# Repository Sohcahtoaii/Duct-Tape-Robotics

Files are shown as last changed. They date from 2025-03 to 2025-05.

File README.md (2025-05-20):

Robot pour la RoboCup – Catégorie Rescue Line Junior

Les fichiers de conception mécanique (CAO) ainsi que ceux de la carte électronique sont disponibles dans ce dépôt.

Une liste complète des pièces utilisées, avec des liens vers les composants, est également fournie.
Cependant, il est fortement recommandé de vérifier les empreintes (footprints) et les dimensions avant tout achat, afin d’éviter les erreurs de compatibilité.

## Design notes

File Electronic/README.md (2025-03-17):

Carte électronique du robot, liste des composants et librairy avec les componsants utilisés

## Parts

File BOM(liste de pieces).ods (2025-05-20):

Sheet: Feuille 1
Mecanique | ref | ref schema | nb | prix | cumul | lien
Roulement à billes 686-ZZ |  | nf | 1 | 2.9 | 2.9
Vis m3 |  | nf | 1 | 1.59 | 1.59
Insert a chaud |  | nf | 2 | 1.95 | 3.9
 |  |  |  |  | 0
Carte mere |  |  |  |  | 0
Batterie/ connecteur |  |  |  |  | 0
XT60PW male |  | J7 | 1 | 3.59 | 3.59 | Lien (https://fr.aliexpress.com/item/1005005383209263.html?mp=1)
led allumage | smd 0805 | D7 | 1 | 2.99 | 2.99 | Lien (https://fr.aliexpress.com/item/1005005226854182.html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)
Resistance | smd 0805 | R8 | 1 | 3.95 | 3.95 | Lien (https://fr.aliexpress.com/item/1005006823361841.html?sourceType=1)
Alim 5v |  |  |  |  | 0
TPS5431DDA | regulateur linéaire | U1 | 1 | 4.49 | 4.49 | Lien (https://fr.aliexpress.com/item/1005007968402584.html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)
Condensateur | smd0805 10nF78mOhm | C1 | 1 |  | 0 | Lien (https://fr.aliexpress.com/item/1005002782324319.html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)
Condensateur | smd 0805 22uF2mOhm | C6/C10 | 2 |  | 0 | Lien (https://fr.aliexpress.com/item/1005002782324319.html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)
Condensateur polarisé | CP_Elec_10x12.6 330uF25mOhm | C2 | 1 | 3.6 | 3.6 | Lien (https://fr.aliexpress.com/item/1005002964957462.html?productId=1005002964957462)
Inductor | 15uH32mOhm | L2 | 1 | 1.43 | 1.43 | Lien (https://fr.aliexpress.com/item/1005006170108324.html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)
Schottky diode | 450mV3A | D1 | 1 | 2.34 | 2.34 | Lien (https://fr.aliexpress.com/item/1005008728420045.html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)
Resistance | smd 0805 10K | R1 | 1 |  | 0 | Lien (https://fr.aliexpress.com/item/1005006823361841.html?sourceType=1)
Resistance | smd 0805 3.24K | R2 | 1 |  | 0 | Lien (https://fr.aliexpress.com/item/1005006823361841.html?sourceType=1)
Alim3,3v |  |  |  |  | 0
TPS5431DDA | regulateur linéaire | U3 | 0 | 4.49 | 0 | Lien (https://fr.aliexpress.com/item/1005007968402584.html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)
Condensateur | 4.7uF3mOhm | C5/c8/c9 | 1 |  | 0 | Lien (https://fr.aliexpress.com/item/1005002782324319.html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)
Condensateur | 10nF78mOhm | C3 | 1 |  | 0 | Lien (https://fr.aliexpress.com/item/1005002782324319.html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)
Condensateur polarisé | 560uF 9mOhm | C4 | 1 | 2.17 | 2.17 | Lien (https://fr.aliexpress.com/item/1005006235242712.html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)
Inductor | 10uH31mOhm | L1 | 1 | 1.6 | 1.6 | Lien (https://fr.aliexpress.com/item/4001191021559.html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)
Schottky diode | 500mV3A | D2 | 1 | 1.74 | 1.74 | Lien (https://fr.aliexpress.com/item/1005008728420045.html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)
Resistance | smd0805 10k | R3 | 1 |  | 0 | Lien (https://fr.aliexpress.com/item/1005006823361841.html?sourceType=1)
Resistance | smd0805 5,9k | R4 | 1 |  | 0 | Lien (https://fr.aliexpress.com/item/1005006823361841.html?sourceType=1)
 |  |  |  |  | 0
Port usb |  |  |  |  | 0
port usb | USB_C_ N 16Pin |  | 1 | 1.78 | 1.78 | Lien (https://fr.aliexpress.com/item/1005007419369264.html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)
Resistance | 0805 5,1k | r5/r6 | 2 |  | 0 | Lien (https://fr.aliexpress.com/item/1005006823361841.html?sourceType=1)
Bidirectional transient-voltage-suppression diode | bidirectional tvs LESD5D5.0CT1G | D4/D5/D6 | 3 | 2.99 | 8.97 | Lien (https://fr.aliexpress.com/item/1005007089592096.html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)
Schottky diode | B130-E3 | D3 | 1 | 5.34 | 5.34 | Lien (https://fr.aliexpress.com/item/1005008617442777.html?mp=1)
Bouton boot |  |  |  |  | 0
push button traversant | push button | SW1 | 1 | 0.96 | 0.96 | Lien (https://fr.aliexpress.com/item/1005006046180384.html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)
Condensateur | 1uF/10V/10%/X5R/C0603 | C12 | 1 |  | 0 | Lien (https://fr.aliexpress.com/item/1005002782324319.html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)
Resistance | 10k smd0805 | R7 | 1 |  | 0 | Lien (https://fr.aliexpress.com/item/1005006823361841.html?sourceType=1)
Bouton rst |  |  |  |  | 0
push button traversant | push button | SW2 | 1 |  | 0 | Lien (https://fr.aliexpress.com/item/1005006046180384.html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)
Condensateur | 1uF/10V/10%/X5R/C0603 | C7 | 1 |  | 0 | Lien (https://fr.aliexpress.com/item/1005002782324319.html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)
Resistance | 10k smd0805 | R19 | 1 |  | 0 | Lien (https://fr.aliexpress.com/item/1005006823361841.html?sourceType=1)
Mesure batterie |  |  |  |  | 0
Resistance | 100k smd 0805 | R9 | 1 |  | 0 | Lien (https://fr.aliexpress.com/item/1005006823361841.html?sourceType=1)
Resistance | 27k smd 0805 | R10 | 1 |  | 0 | Lien (https://fr.aliexpress.com/item/1005006823361841.html?sourceType=1)
Condensateur | 100nF | C11 | 1 |  | 0 | Lien (https://fr.aliexpress.com/item/1005002782324319.html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)
Driver |  |  |  |  | 0
PinSocket_1x07_P2.54mm_Vertical_SMD_Pin1Righ |  |  | 1 | 2.62 | 2.62 | Lien (https://fr.aliexpress.com/item/1005006319376319.html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)
PinSocket_1x07_P2.54mm_Vertical_SMD_Pin1left |  |  | 1 | 2.62 | 2.62 | Lien (https://fr.aliexpress.com/item/1005006319376319.html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)
Capteur |  |  |  |  | 0
Connecteur 11 pin molex picoblade |  | J8 | 1 | 5.59 | 5.59 | Lien (https://fr.aliexpress.com/item/1005006111477998.html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)
Connecteur 4 pin molex picoblade |  | J2 | 1 | 1.35 | 1.35 | Lien (https://fr.aliexpress.com/item/1005006027334406.html?mp=1)
Connecteur 7 pin molex picoblade |  | J9/J10 | 2 | 1.55 | 3.1 | Lien (https://fr.aliexpress.com/item/1005006027334406.html?mp=1)
Connecteur 8 pin molex picoblade |  | J11 | 1 | 1.55 | 1.55 | Lien (https://fr.aliexpress.com/item/1005006027334406.html?mp=1)
capteur de couleur |  |  | 2 | 2.12 | 4.24
capteur de ligne | QTRX-MD-08A |  | 1
Moteur |  |  | 1 | 26.75 | 26.75
bornier a vis |  | j3/j4 | 2 | 1.41 | 2.82 | Lien (https://www.aliexpress.com/store/1102861072?spm=a2g0o.cart.0.0.24a2378dIC0mR0)
Traitement |  |  |  |  | 0
esp32 s3 wroom 2 | esp32 s3 wroom 2 | U2 | 1 | 19.52 | 19.52 | lien (https://www.mouser.fr/ProductDetail/Espressif-Systems/ESP32-S3-WROOM-1-N8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)
 |  |  |  |  | 123.5

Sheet: Feuille 2
Support Moteur | 2 | Impression 3D
Cache moteur | 2 | Impression 3D
Support roue libre | 2 | Impression 3D
Châssis haut | 1 | Découpe laser
Châssis bas | 1 | Découpe laser
Axe roue arriere | 2(pièce de rechange conseillé) | Impression 3D
roue holonome GTF robot | 2 | Acheté
Roue avant personnalisé | 2 | Usinage CNC Moulage silicone (Département GMP iut Bordeaux)
adaptateur axe roue avant part 1 | 2 | Impression 3D
adaptateur axe roue avant part 2 | 2 | Impression 3D
Support capteur de ligne | 1 | Impression 3D
Support capteur ultrason | 1 | Impression 3D
Support Batterie | 1 | Impression 3D
Fermeture support batterie | 1 | Impression 3D
Roulement a bille SBC686ZZ | 4 | Acheté
Entretoise M/F 45mm m3 | 4 | Acheté
Entretoise M/F 15mm m3 | 4 | Acheté
Vis M3x6 | env.70 | Acheté
Vis M3x8 | env.10 | Acheté
Insert à chaud M3 | env.40 | Acheté
Moteur Modelcraft RB350030-0A101R 1:30 | 2 | Acheté

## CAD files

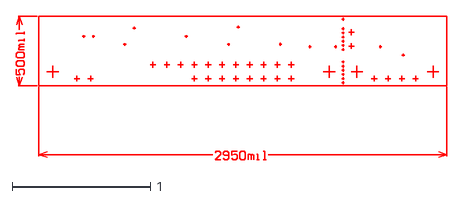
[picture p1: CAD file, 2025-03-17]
CAO/Used model/irs02a02-drill.dxf
3.11 x 1.04

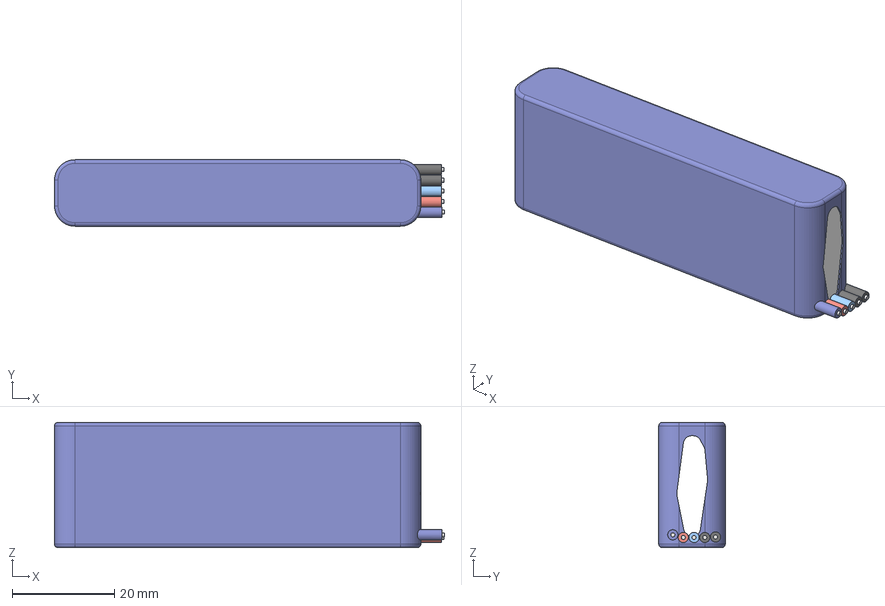
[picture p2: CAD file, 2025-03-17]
CAO/Used model/Battery.step
76.2 x 13.0 x 24.5 mm

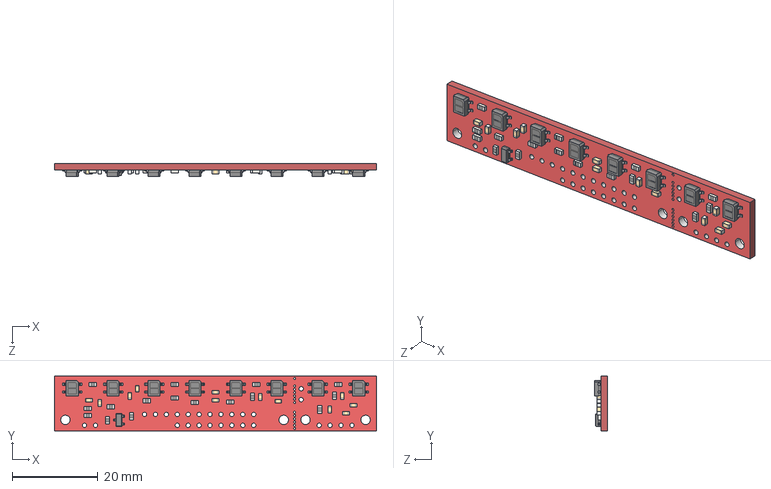
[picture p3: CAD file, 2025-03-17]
CAO/Used model/qtr-8rc-reflectance-sensor-array.step
74.9 x 12.7 x 3.07 mm

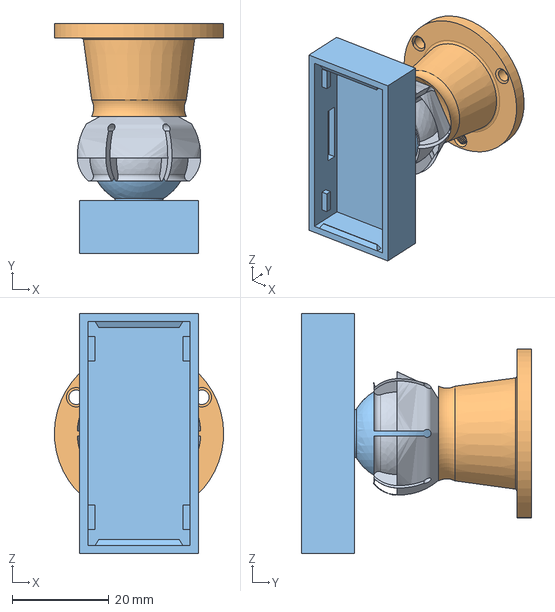
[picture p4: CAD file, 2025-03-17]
CAO/Used model/Ultrasonic Sensor Hc-SR04 adjustable case.step
34.9 x 47.5 x 49.5 mm

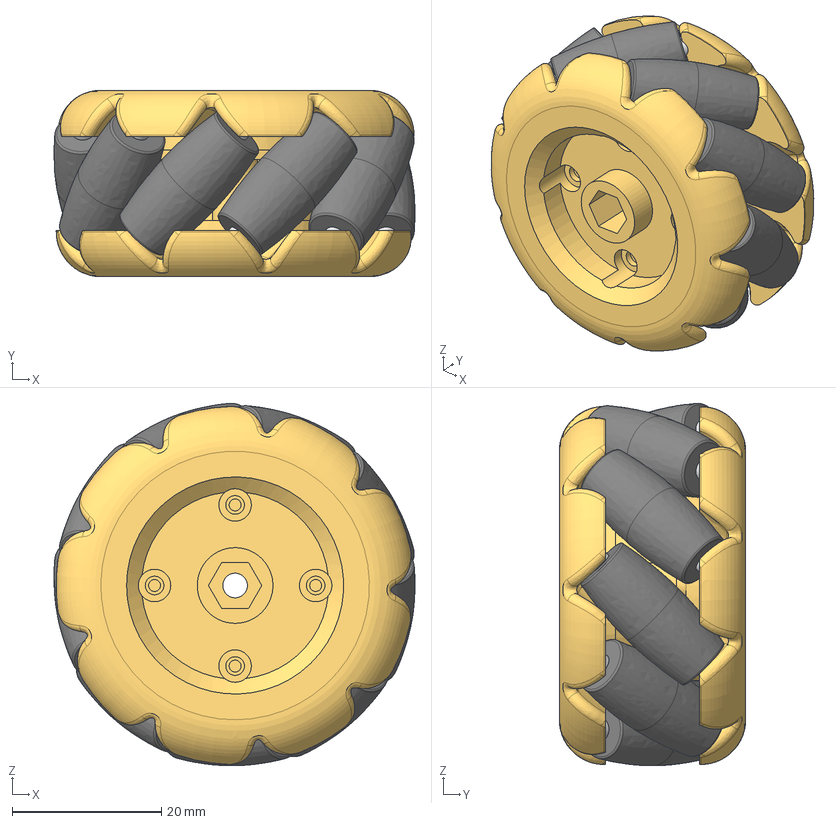
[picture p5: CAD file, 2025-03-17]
CAO/Used model/Mecanum Left v5.step
48.4 x 25.0 x 48.6 mm
Side1
Side 2
Roller x 9

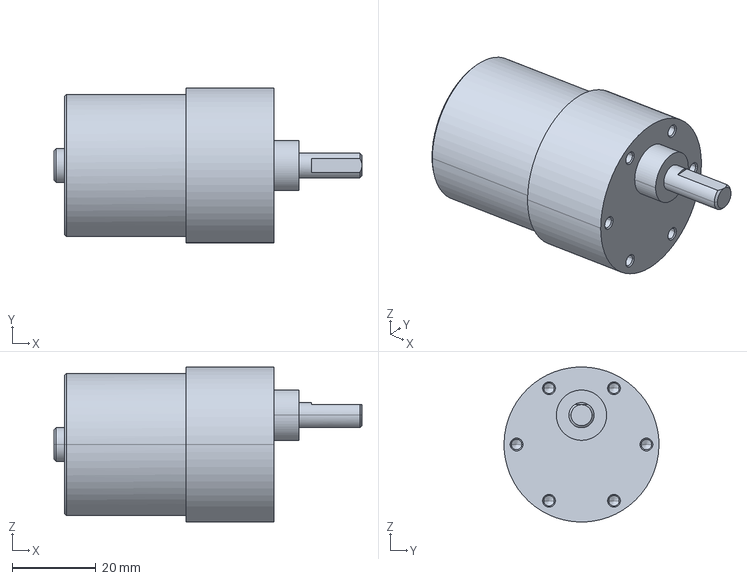
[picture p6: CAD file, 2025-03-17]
CAO/Used model/moteur.stp
73.5 x 37.0 x 37.0 mm

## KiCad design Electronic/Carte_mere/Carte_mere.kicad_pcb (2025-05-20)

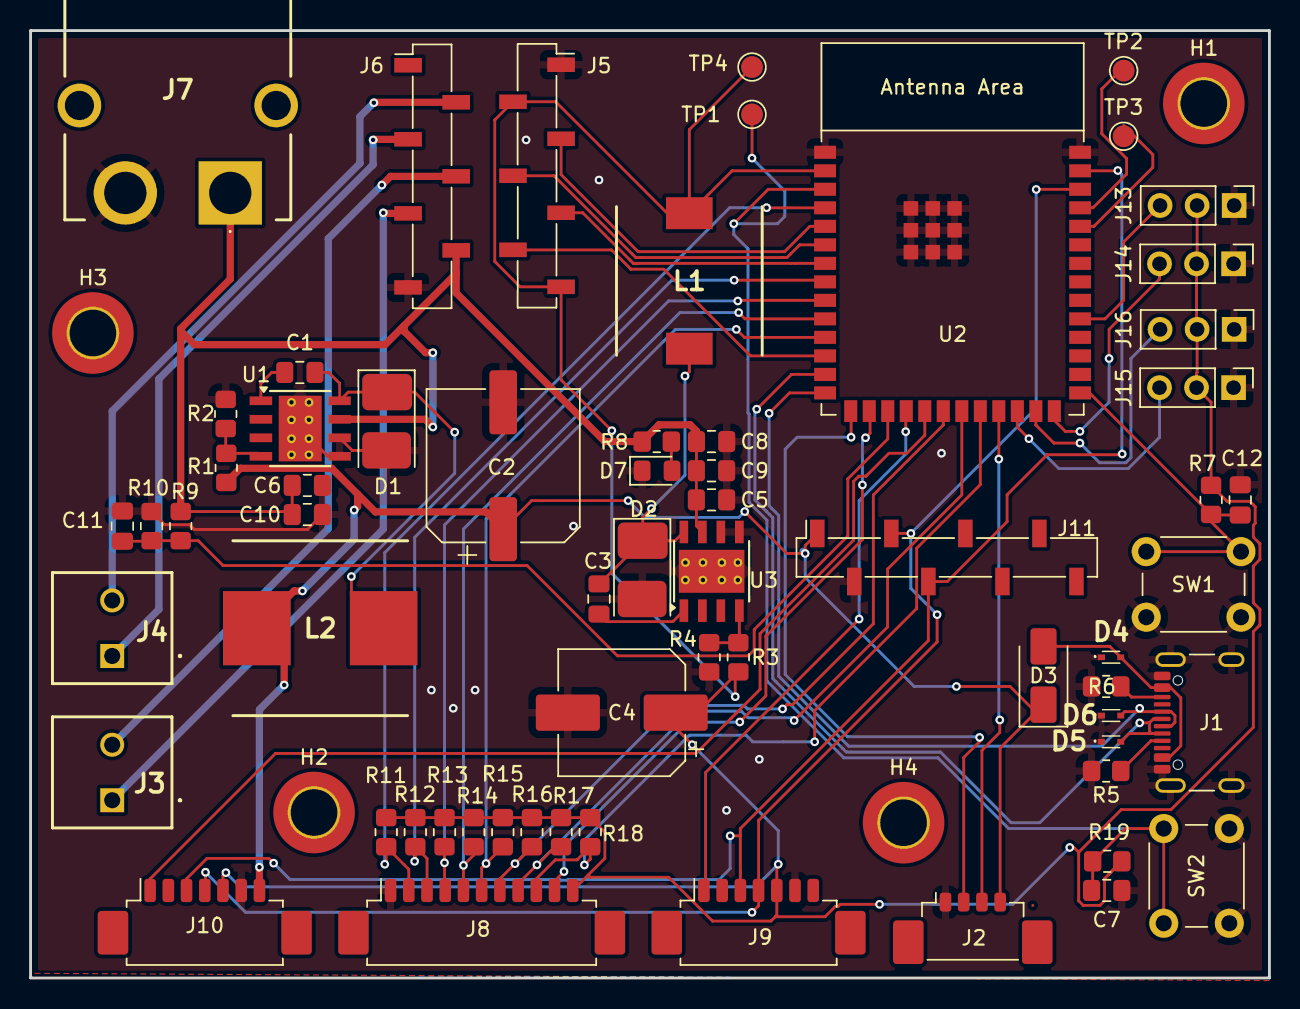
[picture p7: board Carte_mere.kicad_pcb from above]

Board: 2 copper layers, 85.0 x 65.0 mm, 68 parts (0 on the bottom side), 48 nets.

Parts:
C1, C3: 10nF78mOhm; C_0805_2012Metric_Pad1.18x1.45mm_HandSolder
C2: 330uF25mOhm; CP_Elec_10x12.6
C4: 560uF 9mOhm; CP_Elec_8x10.5
C5, C8, C9: 4.7uF3mOhm; C_0805_2012Metric_Pad1.18x1.45mm_HandSolder
C6, C10: 22uF2mOhm; C_0805_2012Metric_Pad1.18x1.45mm_HandSolder
C7, C12: 1uF/10V/10%/X5R/C0603; C_0805_2012Metric_Pad1.18x1.45mm_HandSolder
C11: 100nF; C_0805_2012Metric_Pad1.18x1.45mm_HandSolder
D1: 450mV3A; B340LA
D2: 500mV3A; B340LA
D3: B130-E3; D_SMA
D4, D5, D6: LESD5D5.0CT1G; LESD5D50CT1G
D7: LED; LED_0805_2012Metric_Pad1.15x1.40mm_HandSolder
H1, H2, H3, H4: MountingHole_Pad_MP; MountingHole_3.2mm_M3_DIN965_Pad_TopBottom
J1: USB_C_Receptacle_USB2.0_14P; USB_C_Receptacle_GCT_USB4105-xx-A_16P_TopMnt_Horizontal
J2: Conn_01x04; Molex_PicoBlade_53398-0471_1x04-1MP_P1.25mm_Vertical
J3, J4: Conn_01x02; 2843922
J5: Conn_01x07; PinSocket_1x07_P2.54mm_Vertical_SMD_Pin1Right
J6: Conn_01x07; PinSocket_1x07_P2.54mm_Vertical_SMD_Pin1Left
J7: xt60pm; XT60PWM
J8: Conn_01x11; Molex_PicoBlade_53261-1171_1x11-1MP_P1.25mm_Horizontal
J9, J10: Conn_01x07; Molex_PicoBlade_53261-0771_1x07-1MP_P1.25mm_Horizontal
J11: Conn_01x08; PinSocket_1x08_P2.54mm_Vertical_SMD_Pin1Right
J13, J14, J15, J16: Conn_01x03; PinHeader_1x03_P2.54mm_Vertical
L1: 10uH31mOhm; INDPM102100X510N
L2: 15uH32mOhm; INDPM120120X620N
R1: 10K; R_0805_2012Metric_Pad1.20x1.40mm_HandSolder
R2: 3.24K; R_0805_2012Metric_Pad1.20x1.40mm_HandSolder
R3, R7, R19: 10k; R_0805_2012Metric_Pad1.20x1.40mm_HandSolder
R4: 5.9k; R_0805_2012Metric_Pad1.20x1.40mm_HandSolder
R5, R6: 5.1k; R_0805_2012Metric_Pad1.20x1.40mm_HandSolder
R8: R; R_0805_2012Metric_Pad1.20x1.40mm_HandSolder
R9: 100k; R_0805_2012Metric_Pad1.20x1.40mm_HandSolder
R10: 27k; R_0805_2012Metric_Pad1.20x1.40mm_HandSolder
R11, R12, R13, R14, R15, R16, R17, R18: 47k; R_0805_2012Metric_Pad1.20x1.40mm_HandSolder
SW1: push button; SW_PUSH_6mm_H5mm
SW2: push button RST; SW_PUSH_6mm_H5mm
TP1: TestPoint; TestPoint_Pad_D1.5mm
TP2: TX; TestPoint_Pad_D1.5mm
TP3: RX; TestPoint_Pad_D1.5mm
TP4: 3.3V; TestPoint_Pad_D1.5mm
U1, U3: TPS5431DDA; TI_SO-PowerPAD-8_ThermalVias
U2: ESP32-S3-WROOM-2

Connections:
+3.3V: C4.1, J5.2, J5.7, J8.11, J9.5, J10.5, J13.2, J14.2, J15.2, J16.2, L1.2, R3.1, R7.2, R11.1, R12.1, R13.1, R14.1, R15.1, R16.1, R17.1, R18.1, R19.2, TP4.1, U2.2 (3V3)
+5V: C2.1, D3.1 (K), J2.4, J10.7, J11.1, L2.2, R1.1
BOOT: C12.1, R7.1, SW1.1, U2.27 (GPIO0/BOOT)
DRV1G: J5.4, U2.6 (GPIO6/TOUCH6/ADC1_CH5)
DRV1P: J5.3, U2.5 (GPIO5/TOUCH5/ADC1_CH4)
DRV2G: J5.6, U2.12 (GPIO8/TOUCH8/ADC1_CH7/SUBSPICS1)
DRV2P: J5.5, U2.7 (GPIO7/TOUCH7/ADC1_CH6)
EN: C7.1, R19.1, SW2.1, TP1.1, U2.3 (EN)
GND: C2.2, C4.2, C5.1, C6.1, C7.2, C8.1, C9.1, C10.1, C11.1, C12.2, D1.2 (A), D2.2 (A), D4.1 (A1), D5.1 (A1), D6.1 (A1), D7.1 (K), J1.A1 (GND), J1.A12 (GND), J1.B1 (GND), J1.B12 (GND), J1.S1 (SHIELD), J2.1, J5.1, J6.7, J7.2, J8.1, J9.6, J10.6, J11.2, J13.1, J14.1, J15.1, J16.1, R2.2, R4.2, R5.2, R6.2, R10.2, SW1.2, SW2.2, U1.5 (EN), U1.6 (GND), U1.9 (GNDPAD), U2.1 (GND), U2.40 (GND), U2.41 (GND), U3.5 (EN), U3.6 (GND), U3.9 (GNDPAD)
LED1: J9.1, U2.18 (GPIO10/TOUCH10/ADC1_CH9/FSPICS0/FSPIIO4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)
LED2: J10.1, U2.19 (GPIO11/TOUCH11/ADC2_CH0/FSPID/FSPIIO5/S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)
LIPO11V1: C5.2, C6.2, C8.2, C9.2, C10.2, J6.6, J7.1, R8.1, R9.1, U1.7 (VIN), U3.7 (VIN)
M1+: J3.1, J6.5
M1-: J3.2, J6.4
M2+: J4.1, J6.3
M2-: J4.2, J6.2
NB1: J8.2, R11.2, U2.4 (GPIO4/TOUCH4/ADC1_CH3)
NB2: J8.3, R12.2, U2.8 (GPIO15/U0RTS/ADC2_CH4/XTAL_32K_P)
NB3: J8.4, R13.2, U2.9 (GPIO16/U0CTS/ADC2_CH5/XTAL_32K_N)
NB4: J8.5, R14.2, U2.10 (GPIO17/U1TXD/ADC2_CH6)
NB5: J8.6, R15.2, U2.11 (GPIO18/U1RXD/ADC2_CH7/CLK_OUT3)
NB6: J8.7, R16.2, U2.20 (GPIO12/TOUCH12/ADC2_CH1/FSPICLK/FSPIIO6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)
NB7: J8.8, R17.2, U2.21 (GPIO13/TOUCH13/ADC2_CH2/FSPIQ/FSPIIO7/S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)
NB8: J8.9, R18.2, U2.22 (GPIO14/TOUCH14/ADC2_CH3/FSPIWP/FSPIDQS/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)
unnamed: C1.2, D1.1 (K), L2.1, U1.8 (PH)
unnamed: C3.2, D2.1 (K), L1.1, U3.8 (PH)
unnamed: D3.2 (A), D4.2 (A2), J1.A4 (VBUS), J1.A9 (VBUS), J1.B4 (VBUS), J1.B9 (VBUS)
unnamed: D7.2 (A), R8.2
unnamed: J1.A5 (CC1), R5.1
unnamed: J1.B5 (CC2), R6.1
unnamed: C1.1, U1.1 (BOOT)
unnamed: R1.2, R2.1, U1.4 (VSENSE)
unnamed: TP3.1, U2.36 (U0RXD/GPIO44/CLK_OUT2)
unnamed: TP2.1, U2.37 (U0TXD/GPIO43/CLK_OUT1)
unnamed: C3.1, U3.1 (BOOT)
unnamed: R3.2, R4.1, U3.4 (VSENSE)
RAB1: J13.3, U2.31 (GPIO38/FSPIWP/SUBSPIWP)
RAB2: J14.3, U2.26 (GPIO45)
RAB3: J15.3, U2.24 (GPIO47/SPICLK_P/SUBSPICLK_P_DIFF)
RAB4: J16.3, U2.25 (GPIO48/SPICLK_N/SUBSPICLK_N_DIFF)
SCL: J9.4, J10.4, J11.3, U2.38 (GPIO2/TOUCH2/ADC1_CH1)
SDA: J9.3, J10.3, J11.4, U2.39 (GPIO1/TOUCH1/ADC1_CH0)
USB_D+: D6.2 (A2), J1.A6 (D+), J1.B6 (D+), U2.14 (GPIO20/U1CTS/ADC2_CH9/CLK_OUT1/USB_D+)
USB_D-: D5.2 (A2), J1.A7 (D-), J1.B7 (D-), U2.13 (GPIO19/U1RTS/ADC2_CH8/CLK_OUT2/USB_D-)
echo: J2.2, U2.15 (GPIO3/TOUCH3/ADC1_CH2)
indiclipo: C11.2, R9.2, R10.1, U2.17 (GPIO9/TOUCH9/ADC1_CH8/FSPIHD/SUBSPIHD)
ledon: J8.10, U2.16 (GPIO46)
trig: J2.3, U2.23 (GPIO21)

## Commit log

2025-04-09 Delete Electronic/Carte_mere directory
    delete before reupload
    [Carte_mere.kicad_pcb, Carte_mere.kicad_sch]
2025-04-09 final peut êtres
    [Carte_mere.kicad_pcb, Carte_mere.kicad_sch]
2025-05-19 Add MotorLib
2025-05-20 Rename piece robot.ods to BOM(liste de pieces.ods
    [BOM(liste de pieces.ods]
2025-05-20 Rename BOM(liste de pieces.ods to BOM(liste de pieces).ods
    [BOM(liste de pieces).ods]
